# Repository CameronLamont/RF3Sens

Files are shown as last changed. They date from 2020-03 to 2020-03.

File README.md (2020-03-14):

<pre>
// ##################################################### ###############################################
// RF3Sens (RoboForum triangulation range sensor)
// http://roboforum.ru/forum107/topic15929.html (official language for this forum - russian)
// MIT License
// 2015-2016
// Dmitry Lilik (aka Dmitry__ @ RoboForum.ru)
// Andrey Pozhogin (aka dccharacter @ RoboForum.ru)
// Sergey Taranenko (aka setar @ RoboForum.ru)
// ##################################################### ###############################################
</pre>

High precision (0.01+ mm) optical barrier to the table surface of 3D printers.
Based on the analysis of the illumination pattern of the CCD matrix (from the mouse) by scattered radiation from a laser source,
according to the principle of a triangle, at predetermined installation angles of the laser and the matrix.
It does not depend on the type of table material (theoretically, the technique is still in development).

The claimed accuracy has already been obtained by practical means on prototypes.
<pre>
vvv ========= 3D printer printing carriage =============== vvv
  - sensor ------- laser - (sensor circuit board)
         \\\\ ||||
            \ | |
             \ | |
              \ | |
               \ | |
                \ | |
                 \ | |
                  \ | |
                   \ | |
                    \ | |
                     \ | |
------ level ------- * --- tripping -------------------
                      | \ |
                      | \
    here the sensor does not see the laser spot and there is no response
^^^ ================ 3D printer table ==================== ^^^
</pre>

* Schemes for connecting different arduin (and other microcontrollers) in the doc folder

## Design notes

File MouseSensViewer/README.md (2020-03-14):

Viewer of data from CCDs of mouse matrices and visualization of pictures on a computer.
For:
RoboForum triangulation range sensor
http://roboforum.ru/forum107/topic15929.html (official language for this forum - russian)

## Linux build

'' '
mkdir / home / user-name / tmp / MouseViewer
cd / home / user-name / tmp / MouseViewer
qmake /path/to/RF3Sens/MouseSensViewer/Viewer.pro
make
'' '

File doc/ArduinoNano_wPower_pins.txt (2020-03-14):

power mode of the sensor and the laser from the legs of the microcontroller (we supply power to the desired legs)

--- ADNS-2610 sensor ---
OSC_IN (1 pin): on quartz 24MHz
OSC_OUT (2 pin): on quartz 24MHz
MOSI (3 pin): PB5 D13
SCK (4 pin): PB2 D10
GND (6 pin): PB4 D12
VDD (7 pin): PB3 D11
REFA (8 pin): via 2.2MKF capacitor to ground (6 pin)

--- 5mW laser diode ---
Laser VCC: PD2 D2
Laser GND: Through 100 Ohm Resistance to Ground

--- exit ---
MCU POWER (sensor + 5V): VCC
MCU GND (sensor GND): GND
led (sensor signal): PC5 A5

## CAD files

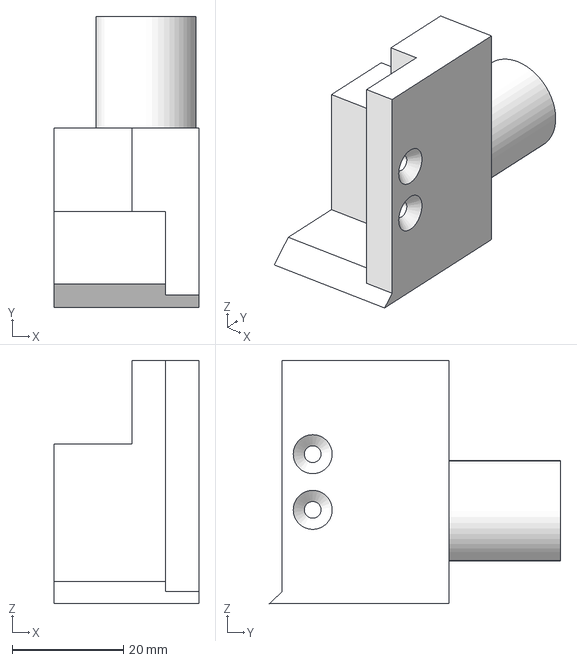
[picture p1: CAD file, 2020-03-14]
Models/universal_to_tube18mm.step
26.0 x 52.3 x 43.7 mm

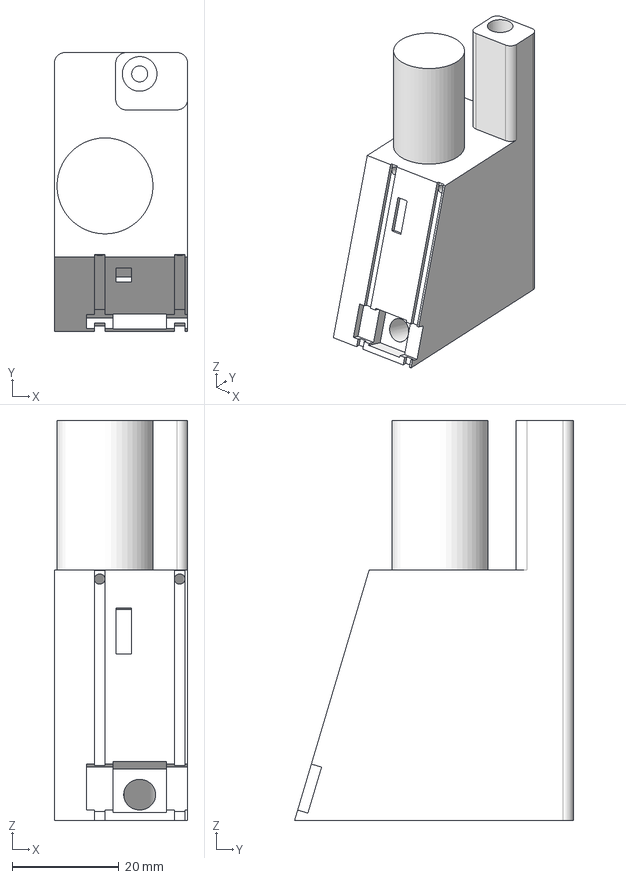
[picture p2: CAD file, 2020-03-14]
Models/ArduinoNano_wPower_tube18mm.step
25.0 x 52.3 x 75.0 mm

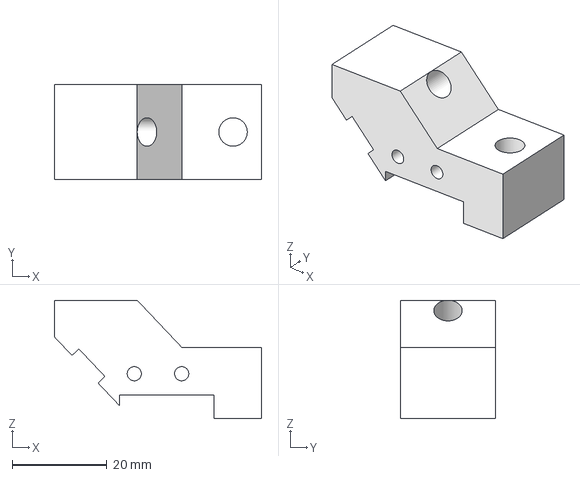
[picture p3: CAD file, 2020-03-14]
Models/Digispark_universal.step
43.7 x 20.0 x 25.0 mm

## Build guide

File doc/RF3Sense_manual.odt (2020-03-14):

Synchronization with printer electronics via g-code (trigger pin)

Link: http://roboforum.ru/post343825.html?hilit=trigger#p343825

G1 F2000 5 ;travel to initial position (absolute) z
G4 S1;sleep for 1 sec
M42 P4 S255;set trigger pin 4 HIGH (servo 4 signal pin)
G1 F60 0;travel to end position slowly
M400 ;wait for previous command to complete
M42 P4 S0;set trigger pin LOW

Синхронизация с электроникой принтера через g-code (trigger pin)

ссылка: http://roboforum.ru/post343825.html?hilit=trigger#p343825

G1 F2000 Z5 ;travel to initial position (absolute) <- здесь z устанавливаешь равным полному ходу датчика
G4 S1 ;sleep for 1 sec
M42 P4 S255 ;set trigger pin 4 HIGH (servo 4 signal pin)
G1 F60 Z0 ;travel to end position slowly
M400 ;wait for previous command to complete
M42 P4 S0 ;set trigger pin LOW

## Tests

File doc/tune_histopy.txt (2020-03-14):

Sketch uses 1 268 bytes (4%) of program storage space. Maximum is 30 720 bytes.
Global variables use 236 bytes (11%) of dynamic memory, leaving 1 812 bytes for local variables. Maximum is 2 048 bytes.

программный spi
Sketch uses 912 bytes (2%) of program storage space. Maximum is 30 720 bytes.
Global variables use 235 bytes (11%) of dynamic memory, leaving 1 813 bytes for local variables. Maximum is 2 048 bytes.

SoftSerial
Sketch uses 3 012 bytes (50%) of program storage space. Maximum is 6 012 bytes.
Global variables use 129 bytes of dynamic memory.
замена SoftSerial на SendOnlySoftwareSerial
Sketch uses 1 878 bytes (31%) of program storage space. Maximum is 6 012 bytes.
Global variables use 42 bytes of dynamic memory.

Sketch uses 4 468 bytes (14%) of program storage space. Maximum is 30 720 bytes.
Global variables use 254 bytes (12%) of dynamic memory, leaving 1 794 bytes for local variables. Maximum is 2 048 bytes.
без Serial.println(String(Frame...
Sketch uses 2 866 bytes (9%) of program storage space. Maximum is 30 720 bytes.
Global variables use 247 bytes (12%) of dynamic memory, leaving 1 801 bytes for local variables. Maximum is 2 048 bytes.

Выпилил ненужный:
Frame[(ARRAY_WIDTH * ARRAY_HEIGHT)+1] = 0xff;  // frame data is 0..63 or 0..127 so delimiter 255 is safe

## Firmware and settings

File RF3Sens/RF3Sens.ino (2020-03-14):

//###########################################################################################
// RF3Sens (RoboForum triangulation range sensor)
// http://roboforum.ru/forum107/topic15929.html (official language for this forum - russian)
// MIT License
// 2015-2016
// Дмитрий Лилик (aka Dmitry__ @ RoboForum.ru)
// Андрей Пожогин (aka dccharacter  @ RoboForum.ru)
// Сергей Тараненко (aka setar @ RoboForum.ru)
//###########################################################################################

#include "Config.h"
#if defined(DEBUG_TYPE) && defined(SOFTWARE_SERIAL)
  #include <SendOnlySoftwareSerial.h>
#endif //#if defined(DEBUG_TYPE) && defined(SOFTWARE_SERIAL)

byte ADNS_read(uint8_t address);
void ADNS_reset(void);
void ADNS_write(uint8_t addr, uint8_t data);
inline void params_grab(uint8_t *buffer, uint8_t ifReset);
inline void pixel_grab(uint8_t *buffer, uint16_t nBytes); 
inline void pixel_and_params_grab(uint8_t *buffer);
inline uint8_t single_line_grab(uint8_t *buffer);
void RefrPowerLaser(uint16_t power, uint16_t value, uint16_t halfDev);
void ByteToString(uint8_t a);
void Uint16ToString(uint16_t a);

unsigned char Str[5];
int16_t RegPowLaser = 0;

void setup(){
  pinMode(3, OUTPUT);
  TCCR2A = 0;
  TCCR2B = 0;
  TCCR2A = _BV(COM2B1) | _BV(WGM21) | _BV(WGM20);
  TCCR2B = _BV(CS20); // no prescaler
  OCR2B = 50;

  pinMode(A5, INPUT);

  //set pin I/O direction
#if defined(USE_NCS)
  PIN_OUTPUT(NCS);
  PIN_HIGH(NCS);
#endif //USE_NCS
  PIN_OUTPUT(LED);
  PIN_HIGH(LED);
#if defined(DEBUG_TYPE) && defined(TRIG_PIN)
  PIN_INPUT(TRIG);
#endif //defined(DEBUG_TYPE) && defined(TRIG_PIN)


  PIN_OUTPUT(laser1_vcc);
  PIN_OUTPUT(laser2_vcc);
  PIN_OUTPUT(laser_pwm);
  analogWrite(9, 0); //preset all analogWrite values so I can just later change OCR1A

//initialize SPI
  PIN_OUTPUT(NCLOCK);
  PIN_HIGH(NCLOCK);
  PIN_OUTPUT(SDIO);
  PIN_LOW(SDIO);

//#if defined(DEBUG_TYPE)
  SERIAL_OUT.begin(SERIAL_SPEED);
//#endif // defined(DEBUG_TYPE)

  delay(1000);
  ADNS_reset();
}

void loop(){
//###########################################################################################
// standard sensor mode for 3D printer
#ifndef DEBUG_TYPE
  uint8_t Frame[NUM_PIXS + 7] = {0};
  uint8_t dataSum, dataSqual, lineMax;
  
  PIN_LOW(LED);

  PIN_LOW(laser1_vcc); //enable base laser
  analogWrite(9,130);

  while(1){
    params_grab(Frame, 1);
    dataSum = Frame[3];
    dataSqual = Frame[0];
    ByteToString(RegPowLaser); SERIAL_OUT.write(Str[2]); SERIAL_OUT.write(Str[1]);
      SERIAL_OUT.write(Str[0]); SERIAL_OUT.write(0x09);
    ByteToString(dataSum); SERIAL_OUT.write(Str[2]); SERIAL_OUT.write(Str[1]);
      SERIAL_OUT.write(Str[0]); SERIAL_OUT.write(0x09);
    if (dataSqual > 30) {
      lineMax = single_line_grab(Frame);
      ByteToString(lineMax); SERIAL_OUT.write('.'); SERIAL_OUT.write(Str[2]); SERIAL_OUT.write(Str[1]);
        SERIAL_OUT.write(Str[0]); SERIAL_OUT.write(0x0a);
      if (lineMax > 60) {
          PIN_HIGH(LED);
          delay(100);
      }
    }
    RefrPowerLaser(dataSum, 23, 2);
    SERIAL_OUT.write(0x0a);
    
    PIN_LOW(LED);
  }
//###########################################################################################
// debug modes
#else //ifndef DEBUG_TYPE
//-------------------------------------------------------------------------------------------
#if DEBUG_TYPE ==1
//-------------------------------------------------------------------------------------------
  byte Frame[NUM_PIXS + 7] = {0}, dataMax, lineMax;
  byte dataMin, lineMin;
  //uint8_t laserId = 2; // 0 = off; 1 = laser 1; 2 = laser 2; 
  //uint16_t dataShutt;
  
  PIN_LOW(LED);

  PIN_LOW(laser1_vcc); //enable base laser
  PIN_HIGH(laser2_vcc); //disable matrix laser
  analogWrite(9,130);

  while(1){
    //pixel_and_params_grab(Frame);
    //dataMax = Frame[NUM_PIXS + 1];
    //lineMax = Frame[NUM_PIXS + 0];
    //lineMin = Frame[NUM_PIXS + 3];

    //RegPowLaser = (uint8_t)(analogRead(A5) >> 2);    
    //OCR2B = RegPowLaser;
    OCR2B += 1;
   //   }
     /* if (lineMax > 22) { //bingo!
        PIN_HIGH(LED);
        delay(200);
      } else {
        PIN_LOW(LED);
      }*/
    delay(1);
    //} else {
    //  PIN_LOW(LED);
    //}
    
    //SERIAL_OUT.write(Frame, NUM_PIXS + 7); delay(2);// send frame in raw format
  }
//-------------------------------------------------------------------------------------------
#elif DEBUG_TYPE ==2
//-------------------------------------------------------------------------------------------
  byte Frame[NUM_PIXS + 7];

  byte data;
  while(1){
    //data = ADNS_read(ADNS_SQUAL);
    data = ADNS_read(ADNS_MAX_PIX);
    //data = ADNS_read(ADNS_PIX_SUM);

    if(data > ADNS_CONST_MAX){
      PIN_LOW(LED);
    }
    else{
      PIN_HIGH(LED);
      pixel_and_params_grab(Frame);
      SERIAL_OUT.write(Frame, NUM_PIXS+7); // send frame in raw format
    }
  }
//-------------------------------------------------------------------------------------------
#elif DEBUG_TYPE ==3
//-------------------------------------------------------------------------------------------
  //Listing for spreadsheets: In the header of the title, then only the data is separated by a "tab".
  byte Frame[7];
  uint8_t dataMax, lineMax, dataSum;
  //heading
  SERIAL_OUT.println  (F  ("Squal:\tMax:\tMin:\tSum:\tShutter:\tLaserPower:"));
  while(1){
//        RegPowLaser = OCR2B;    
//	OCR2B += 1;
//    params_grab(Frame);

    single_line_grab(Frame);
    dataMax = Frame[NUM_PIXS + 1];
    //dataMin = Frame[NUM_PIXS + 2];
    lineMax = Frame[NUM_PIXS + 0];
    dataSum = Frame[NUM_PIXS + 3];

    //if (dataMax - dataMin > 30) { //laser spot is visible, arm the sensor
    //  if (!(dataMax - dataMin > 40 && lineMax - lineMin > 7)) { //spot has not reached the last line
        //dataShutt = ((*(Frame + NUM_PIXS + 4)) << 8) + *(Frame + NUM_PIXS + 5);
    RefrPowerLaser(dataSum, 35, 2);
    //   }
    if (lineMax > 60) { //22 - bingo!
      PIN_HIGH(LED);
      delay(100);
    } else {
      PIN_LOW(LED);
}
    ByteToString(Frame[NUM_PIXS + 0]); SERIAL_OUT.write(Str[2]); SERIAL_OUT.write(Str[1]); SERIAL_OUT.write(Str[0]); SERIAL_OUT.write(0x09);
    ByteToString(Frame[NUM_PIXS + 1]); SERIAL_OUT.write(Str[2]); SERIAL_OUT.write(Str[1]); SERIAL_OUT.write(Str[0]); SERIAL_OUT.write(0x09);
    //ByteToString(Frame[2]); SERIAL_OUT.write(Str[2]); SERIAL_OUT.write(Str[1]); SERIAL_OUT.write(Str[0]); SERIAL_OUT.write(0x09);
    ByteToString(Frame[NUM_PIXS + 3]); SERIAL_OUT.write(Str[2]); SERIAL_OUT.write(Str[1]); SERIAL_OUT.write(Str[0]); SERIAL_OUT.write(0x09);
    Uint16ToString(Frame[NUM_PIXS + 4] *256 + Frame[NUM_PIXS + 5]);
    SERIAL_OUT.write(Str[4]);
    SERIAL_OUT.write(Str[3]);
    SERIAL_OUT.write(Str[2]);
    SERIAL_OUT.write(Str[1]);
    SERIAL_OUT.write(Str[0]);
    SERIAL_OUT.write(0x09);
    ByteToString(Frame[NUM_PIXS + 6]); SERIAL_OUT.write(Str[2]); SERIAL_OUT.write(Str[1]); SERIAL_OUT.write(Str[0]); SERIAL_OUT.write(0x09);
    SERIAL_OUT.write(0x0d);
    SERIAL_OUT.write(0x0a);

#if SERIAL_SPEED > 115200
      delay(20);
#else
      delay(60);  //delay is longer due to low speed serial
#endif
  }
//-------------------------------------------------------------------------------------------
#elif DEBUG_TYPE ==4
//-------------------------------------------------------------------------------------------
  //As 3rd mode, but by pin_TRIG signal resolution
  byte Frame[7];
  PIN_OUTPUT(gpio1);
  PIN_LOW(gpio1);

  PIN_LOW(laser1_vcc); //enable base laser
  PIN_HIGH(laser2_vcc); //disable matrix laser
  RegPowLaser = 140;
  analogWrite(9, RegPowLaser);

  // start by printing caps
  SERIAL_OUT.println (F  ("Squal:\tMax:\tMin:\tSum:\tShutter:\tLaserPower:"));

  while(1){

    if(PIN_READ(TRIG)){ // each measurement starts with a trigger signal (cocked in g-code)
      
      while(PIN_READ(TRIG));

      params_grab(Frame);

      ByteToString(Frame[0]); SERIAL_OUT.write(Str[2]); SERIAL_OUT.write(Str[1]); SERIAL_OUT.write(Str[0]); SERIAL_OUT.write(0x09);
      ByteToString(Frame[1]); SERIAL_OUT.write(Str[2]); SERIAL_OUT.write(Str[1]); SERIAL_OUT.write(Str[0]); SERIAL_OUT.write(0x09);
      ByteToString(Frame[2]); SERIAL_OUT.write(Str[2]); SERIAL_OUT.write(Str[1]); SERIAL_OUT.write(Str[0]); SERIAL_OUT.write(0x09);
      ByteToString(Frame[3]); SERIAL_OUT.write(Str[2]); SERIAL_OUT.write(Str[1]); SERIAL_OUT.write(Str[0]); SERIAL_OUT.write(0x09);
      Uint16ToString(Frame[4] *256 + Frame[5]);
      SERIAL_OUT.write(Str[4]);
      SERIAL_OUT.write(Str[3]);
      SERIAL_OUT.write(Str[2]);
      SERIAL_OUT.write(Str[1]);
      SERIAL_OUT.write(Str[0]);
      SERIAL_OUT.write(0x09);
      ByteToString(Frame[6]); SERIAL_OUT.write(Str[2]); SERIAL_OUT.write(Str[1]); SERIAL_OUT.write(Str[0]); SERIAL_OUT.write(0x09);
      SERIAL_OUT.write(0x0a);
      SERIAL_OUT.write(0x0d);

#if SERIAL_SPEED > 115200
      delay(20);
#else
      delay(60);  //delay is longer due to low speed serial
#endif

   // after we read the values and sent them to the series, we give the marlin
    // signal of readiness for the next step
    PIN_HIGH(gpio1);
    delay(40);
    PIN_LOW(gpio1);
    }
  }
//-------------------------------------------------------------------------------------------
#elif DEBUG_TYPE ==5
//-------------------------------------------------------------------------------------------
  while(1){
    unsigned int motion = 0;
    //check for movement
    motion = ADNS_read(ADNS_MOTION);
    if (motion > 127){
      //there has been a motion! Print the x and y movements
      SERIAL_OUT.println("X:" + String(ADNS_read(ADNS_DELTA_X)) + " Y:" + String(ADNS_read(ADNS_DELTA_Y)));
    }
  }
//-------------------------------------------------------------------------------------------
#elif DEBUG_TYPE ==6
//-------------------------------------------------------------------------------------------
  uint8_t Frame[7];
  uint8_t laserId = 2; // 0 = off; 1 = laser 1; 2 = laser 2; 
  //заголовок

  SERIAL_OUT.println  (F  ("Squal:\tMax:\tMin:\tSum:\tShutter:\tLaserId:"));
  while(1){
    params_grab(Frame);

  if (laserId == 2) {
	  PIN_HIGH(laser1_vcc);
	  PIN_LOW(laser2_vcc);
	  laserId = 1;
  } else {
	  PIN_HIGH(laser2_vcc);
	  PIN_LOW(laser1_vcc);
	  laserId = 2;
  }
    ByteToString(Frame[0]); SERIAL_OUT.write(Str[2]); SERIAL_OUT.write(Str[1]); SERIAL_OUT.write(Str[0]); SERIAL_OUT.write(0x09);
    ByteToString(Frame[1]); SERIAL_OUT.write(Str[2]); SERIAL_OUT.write(Str[1]); SERIAL_OUT.write(Str[0]); SERIAL_OUT.write(0x09);
    ByteToString(Frame[2]); SERIAL_OUT.write(Str[2]); SERIAL_OUT.write(Str[1]); SERIAL_OUT.write(Str[0]); SERIAL_OUT.write(0x09);
    ByteToString(Frame[3]); SERIAL_OUT.write(Str[2]); SERIAL_OUT.write(Str[1]); SERIAL_OUT.write(Str[0]); SERIAL_OUT.write(0x09);
    Uint16ToString(Frame[4] *256 + Frame[5]);
    SERIAL_OUT.write(Str[4]);
    SERIAL_OUT.write(Str[3]);
    SERIAL_OUT.write(Str[2]);
    SERIAL_OUT.write(Str[1]);
    SERIAL_OUT.write(Str[0]);
    SERIAL_OUT.write(0x09);
    ByteToString(laserId); SERIAL_OUT.write(Str[2]); SERIAL_OUT.write(Str[1]); SERIAL_OUT.write(Str[0]); SERIAL_OUT.write(0x09);
    SERIAL_OUT.write(0x0d);
    SERIAL_OUT.write(0x0a);

#if SERIAL_SPEED > 115200
      delay(20);
#else
      delay(60);  // the delay is longer due to the low speed of Serial
#endif //SERIAL_SPEED > 115200
  }
#endif //DEBUG_TYPE
#endif // #else #ifndef DEBUG_TYPE
}

//###########################################################################################
// the procedures
//-------------------------------------------------------------------------------------------
void RefrPowerLaser(uint16_t power, uint16_t target_value, uint16_t halfDeviation)
{
  //if (abs((int16_t)target_value - (int16_t)power) > halfDeviation) {
    if (power < target_value) {
      RegPowLaser++;
    } else if (power > target_value) {
      RegPowLaser--;
    }
    if (RegPowLaser > 255) {
      RegPowLaser = 255;
    } else if (RegPowLaser < 0) {
      RegPowLaser = 0;
    }
    OCR2B = (uint8_t)RegPowLaser;
  //}
}
//-------------------------------------------------------------------------------------------
void ADNS_reset(void){
#ifdef sens_type_ADNS_5020
  ADNS_write(0x3a,0x5a);
  delay(1000);
  ADNS_write(0x0d, 0x01);  // Set 1000cpi resolution
  delay(1000);
#endif
#if  defined(sens_type_ADNS_2610) || defined(sens_type_ADNS_2620)
  ADNS_write(ADNS_CONF,0x80);
  delay(1000);
  ADNS_write(ADNS_CONF,0x01); //Always awake
  delay(2);
  ADNS_write(ADNS_FRAME_PERIOD, 0xC2); //set framerate to 3000fps
  delay(2);
#endif
}

//-------------------------------------------------------------------------------------------
void ADNS_write(byte address, byte data){
  #if defined(USE_NCS)
    PIN_LOW(NCS);
  #endif
  // send in the address and value via SPI:
  address |= 0x80;  //признак записи адреса
  for (byte i = 0x80; i; i >>= 1){
    PIN_LOW(NCLOCK);
    address & i ? PIN_HIGH(SDIO) : PIN_LOW(SDIO);
    asm volatile ("nop");
    PIN_HIGH(NCLOCK);
  }

  //delayMicroseconds(1);

  for (byte i = 0x80; i; i >>= 1){
    PIN_LOW(NCLOCK);
    data & i ? PIN_HIGH(SDIO) : PIN_LOW(SDIO);
    asm volatile ("nop");
    PIN_HIGH(NCLOCK);
  }
  //t SWW. SPI Time between Write Commands
  delayMicroseconds(ADNS_DELAY_TSWW);

  #if defined(USE_NCS)
    PIN_HIGH(NCS);
  #endif
}

//-------------------------------------------------------------------------------------------
byte ADNS_read(byte address){
  #if defined(USE_NCS)
    PIN_LOW(NCS);
  #endif

  address &= ~0x80;  //data record flag
  for (byte i = 0x80; i; i >>= 1){
    PIN_LOW(NCLOCK);
    address & i ? PIN_HIGH(SDIO) : PIN_LOW(SDIO);
    asm volatile ("nop");
    PIN_HIGH(NCLOCK);
  }

  // prepare io pin for reading
  PIN_INPUT(SDIO);

  // t SRAD. SPI Read Address-Data Delay
  delayMicroseconds(ADNS_DELAY_TSRAD);

  // read the data
  byte data = 0;
  for (byte i = 8; i; i--){
    // tick, tock, read
    PIN_LOW(NCLOCK);
    asm volatile ("nop");
    PIN_HIGH(NCLOCK);
    data <<= 1;
    if (PIN_READ(SDIO)) data |= 0x01;
  }

  #if defined(USE_NCS)
    PIN_HIGH(NCS);
  #endif
  PIN_OUTPUT(SDIO);
  // t SRW & t SRR = 1μs.
  delayMicroseconds(2);
  return data;
}
//-------------------------------------------------------------------------------------------
inline uint8_t single_line_grab(uint8_t *buffer) {

  uint8_t temp_byte;
  //uint16_t nBytes = NUM_PIXS; //18;
  uint16_t nBytes = 18;
  uint8_t linePix = 18;
  uint8_t lineMax = 0;
  //uint8_t lineMin = 255; //determine max and min pix in data read

  //reset the pixel grab counter
  ADNS_write(ADNS_PIX_GRAB, 0x00);

  for (uint16_t count = 0; count < nBytes; count++) {
    while (1) {
      temp_byte = ADNS_read(ADNS_PIX_GRAB);
      if (temp_byte & ADNS_PIX_DATA_VALID) {
        break;
      }
    }
    temp_byte &= ADNS_MASK_PIX;
    *(buffer + count) = temp_byte;  // only n bits are used for data
    if (temp_byte > lineMax) {
      lineMax = temp_byte;
    }
    //if (temp_byte < lineMin) {
    //  lineMin = temp_byte;
    //}
  }

  return lineMax;
}
//-------------------------------------------------------------------------------------------
inline void pixel_grab(uint8_t *buffer, uint16_t nBytes) {
  uint8_t temp_byte;

  //reset the pixel grab counter
  ADNS_write(ADNS_PIX_GRAB, 0x00);

  for (uint16_t count = 0; count < nBytes; count++) {
    while (1) {
      temp_byte = ADNS_read(ADNS_PIX_GRAB);
      if (temp_byte & ADNS_PIX_DATA_VALID) {
        break;
      }
    }
    *(buffer + count) = temp_byte & ADNS_MASK_PIX;  // only n bits are used for data
  }
}
//-------------------------------------------------------------------------------------------
inline void params_grab(uint8_t *buffer, uint8_t ifReset) {
  if (ifReset) {
    uint8_t temp_byte;
    ADNS_write(ADNS_PIX_GRAB, 0x00);
    while (1) {
      temp_byte = ADNS_read(ADNS_PIX_GRAB);
      if (temp_byte & ADNS_PIX_DATA_VALID) {
        break;
      }
    }
  }
  *(buffer + 0) = ADNS_read(ADNS_SQUAL);
  *(buffer + 1) = ADNS_read(ADNS_MAX_PIX);
  *(buffer + 2) = ADNS_read(ADNS_MIN_PIX);
  *(buffer + 3) = ADNS_read(ADNS_PIX_SUM);
  *(buffer + 4) = ADNS_read(ADNS_SHUTTER_UPPER);
  *(buffer + 5) = ADNS_read(ADNS_SHUTTER_LOWER);
  *(buffer + 6) = (uint8_t)RegPowLaser;
}
//-------------------------------------------------------------------------------------------
inline void pixel_and_params_grab(uint8_t *buffer) {
	pixel_grab(buffer, NUM_PIXS);
	params_grab(buffer + NUM_PIXS, 0);
}
//-------------------------------------------------------------------------------------------
void ByteToString(uint8_t a){
  Str[0] = '0';
  Str[1] = '0';
  Str[2] = '0';
  if (!a) return;
  Str[0] = a % 10 + '0'; a /= 10;
  if (!a) return;
  Str[1] = a % 10 + '0'; a /= 10;
  if (!a) return;
  Str[2] = a % 10 + '0';
}
//-------------------------------------------------------------------------------------------
void Uint16ToString(uint16_t a){
  Str[0] = '0';
  Str[1] = '0';
  Str[2] = '0';
  Str[3] = '0';
  Str[4] = '0';
  if (!a) return;
  Str[0] = a % 10 + '0'; a /= 10;
  if (!a) return;
  Str[1] = a % 10 + '0'; a /= 10;
  if (!a) return;
  Str[2] = a % 10 + '0'; a /= 10;
  if (!a) return;
  Str[3] = a % 10 + '0'; a /= 10;
  if (!a) return;
  Str[4] = a % 10 + '0';
}
//-------------------------------------------------------------------------------------------
uint8_t ByteToAscii_h(uint8_t x){
  uint8_t tmpByte;

  tmpByte = (x >> 4) + 0x30;
  if (tmpByte > 0x39) { tmpByte += 0x07; }
  return tmpByte;
}
//-------------------------------------------------------------------------------------------
uint8_t ByteToAscii_l(uint8_t x){
  uint8_t tmpByte;
  tmpByte = (x & 0x0f) + 0x30;
  if (tmpByte > 0x39) { tmpByte += 0x07; }
  return tmpByte;
}

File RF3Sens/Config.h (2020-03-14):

//###########################################################################################
// RF3Sens (RoboForum triangulation range sensor)
// http://roboforum.ru/forum107/topic15929.html (official language for this forum - russian)
// MIT License
// 2015-2016
// Дмитрий Лилик (aka Dmitry__ @ RoboForum.ru)
// Андрей Пожогин (aka dccharacter  @ RoboForum.ru)
// Сергей Тараненко (aka setar @ RoboForum.ru)
//###########################################################################################

/* Config.h */
//###########################################################################################
//        Manual settings
//###########################################################################################
/*
In the absence of a flag DEBUG_TYPE, the program quickly processes resp. register and provides data on led (regular printer operation).
When the DEBUG_TYPE flag is set, data is transmitted via the serial port:
DEBUG_TYPE = 1 Transmission of the image for focusing the lens, number of. byte = ARRAY_WIDTH * ARRAY_HEIGHT
DEBUG_TYPE = 2 For a test of positioning accuracy (dccharacter idea).
                The search for the threshold as in normal mode (speed is important), as soon as the threshold is triggered - issue a picture in the serial port
DEBUG_TYPE = 3 Transmission in text form to the data terminal: Max_Pix, Min_Pix, Pix_Sum, Shutter
DEBUG_TYPE = 4 As the 3rd mode, but by the resolution of the pin_TRIG signal (the log is precisely limited by the z_probe signal)
DEBUG_TYPE = 5 Mouse movement data.
DEBUG_TYPE = 6 Testing the dual laser mode
*/
#define DEBUG_TYPE 1 
#define NUM_SAMPLES_PER_MEASURE 5 //amount of data for 4th mode

/*
Only relevant if there is a DEBUG_TYPE flag
If defined, the software Serial port is used (only one leg for data transfer)
For the Digispark, this is the only option and automatically turns on 1 foot
If not defined, Hardware Serial is used for debugging.
*/
//#define SOFTWARE_SERIAL 1 // at the same time, a sign of software serial and a leg number for data transfer (TX PIN)
#define SERIAL_SPEED 230400

/*
Type of sensor, select one you need
*/
//#define SENS_TYPE_ADNS_5020
//#define SENS_TYPE_ADNS_2610
#define SENS_TYPE_ADNS_2620

/*
Do we use power from the controller
*/
//#define laser_power_via_mcu // laser power mode from the feet of the microcontroller (apply power to the desired legs)
//#define sens_power_via_mcu // sensor power mode from the feet of the microcontroller (we supply power to the desired legs)

/*
Type of controller, select one you need
*/
//#define DIGI_SPARK
//#define ARDUINO_NANO // arduino nano base wiring
//#define ARDUINO_NANO_wPOWER  // wiring the sensor on the arduino nano to power the feet of the microcontroller
#define ARDUINO_NANO_DOUBLE_LASER

/*
Detection algorithm, select the one you need
*/
//#define Algo_MaxPix         // the simplest mode is when the edge of the laser spot begins to appear in the field of view.
                            // the most stable, but the response distance is different for different surface colors
//#define Algo_MaxSqualMA   // Squal maximum detection mode, as the parameter is not stable; smoothing and analysis are introduced through the sliding average
                            // experimental

//###########################################################################################
//        End of manual settings
//###########################################################################################


#if (defined(DIGI_SPARK) && !defined(SOFTWARE_SERIAL)) 
  #error "This board can be used only with SOFTWARE_SERIAL"
#endif

#if DEBUG_TYPE == 5
  #if defined(SENS_TYPE_ADNS_2610) || defined(SENS_TYPE_ADNS_2620)
    #error "This sensor doesn't have a motion register; DEBUG_TYPE 5 is unavailable"
  #endif
#endif


//###########################################################################################
//        Connecting libraries
//###########################################################################################
#if defined(SENS_TYPE_ADNS_5020)
  #include "sens/ADNS_5020.h"
#endif
#if defined(SENS_TYPE_ADNS_2610)
  #include "sens/ADNS_2610.h"
#endif
#if defined(SENS_TYPE_ADNS_2620)
  #include "sens/ADNS_2620.h"
#endif

#if defined(DIGI_SPARK)
#include "boards/Digispark.h"
#endif
#if defined(ARDUINO_NANO)
#include "boards/ArduinoNano.h"
#endif
#if defined(ARDUINON_NANO_wPOWER)
#include "boards/ArduinoNano.h"
#endif
#if defined(ARDUINO_NANO_DOUBLE_LASER)
#include "board_ArduinoNano_doubleLaser.h"
#endif

#if defined(DEBUG_TYPE) && defined(SOFTWARE_SERIAL)
  #include <SendOnlySoftwareSerial.h>
  SendOnlySoftwareSerial MyDbgSerial(SOFTWARE_SERIAL, false); //true allows to connect to a regular RS232 without RS232 line driver
  #define SERIAL_OUT MyDbgSerial
#else
  #define SERIAL_OUT Serial
#endif
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
